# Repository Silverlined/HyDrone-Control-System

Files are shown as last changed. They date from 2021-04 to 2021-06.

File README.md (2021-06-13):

## About the project

This project follows the develepoment of a control system for an unmanned surface vehicle (USV).
It consists of efficient code to read the PWM output of an RC receiver via Pin Change Interrupts and write PWM to the ESCs controlling underwater thrusters.
An IMU sensor is used to keep track of the vehicle's orientation, while Time-of-Flight (ToF) sensors measure the distance to canal walls and control the orientation via PID algorithm.

## Introduction

Inspection of bridges and quay walls, below or above the water line, is the main activity of oQuay.
They conduct inspection in different ways but one of their key instruments is a sonar camera attached to a USV, called the HyDrone.
In order to make recordings of high quality it is important to sail the HyDrone at a constant distance (parallel) to quay walls.
During operation, the position of the vehicle is affected by wind and water currents, making the sonar images blurry.
The lack of a control system to correct the HyDrones orientation is a pitfall in the design and affects the quality of the inspection work.
Moreover, the GoPro camera on the HyDrone has a short transmission range of ~10m.
This becomes a problem when the HyDrone sails further away, losing the video feedback and the control over the camera.
oQuay are looking for something that can guarantee control of the movement of the vehicle and a device that can increase the transmission range of their GoPro camera.

Assembly files are in the relevant repositoty folders.

## MuSCoW

| Must haves | Should haves | Could haves |
|---|---|---|
| Independent adjustment of the orientation of the HyDrone with respect to canal walls | Orientation correction should be smooth with no oscillations | Adjustment mechanism to adapt for different situations - different heights and shapes of canal walls |
| Sailing at a constant distance 70cm~1m | Stable response in spite of wind and water currents | Audible feedback from the control commands - start/stop could be indicated with some type of sound |
| Increased video transmission range to at least 100 meters | Validation with experiments in real canal environment | |
| Increased GoPro control range to at least 100 meters | Developed system should be portable and detachable | |
| Control system must not exceed €100 | Power source of the system should be rechargeable | |
| Real-time transmission of the video signal | Video should be shown on one of the already available displays | |

## Planning

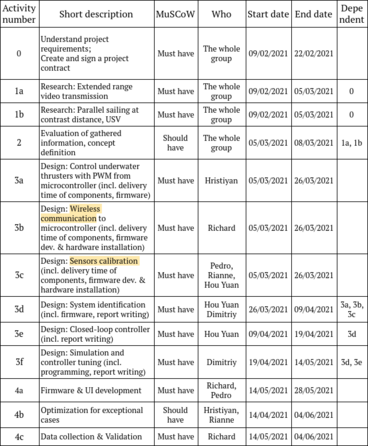
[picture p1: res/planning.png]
Plan


## Pin Change Interrupts

```c
PCICR |= (1 << PCIE0);   // set PCIE0 bit to to enable PCMSK0 scan
PCMSK0 |= (1 << PCINT0); // set PCINT0 (digital pin 8) to trigger an interrupt on state change

// PCINT0_vect is the compiler vector for PCINT0 on PORTB of ATmega328
ISR(PCINT0_vect)
{
  //    // Channel 1==================================
  if (last_channel_1_state == 0 && PINB & B00000001)
  {
    last_channel_1_state = 1;
    timer_channel_1 = micros();
  }
  if (last_channel_1_state == 1 && !(PINB & B00000001))
  {
    last_channel_1_state = 0;
    receiver_input_channel_1 = micros() - timer_channel_1;
  }
  ...
}
```

## FPV System

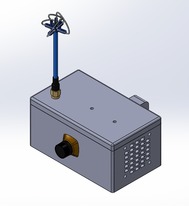
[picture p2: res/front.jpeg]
front


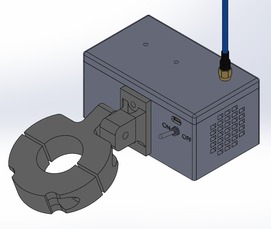
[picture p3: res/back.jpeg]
back


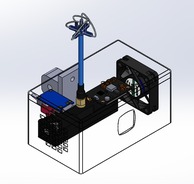
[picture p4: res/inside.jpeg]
inside


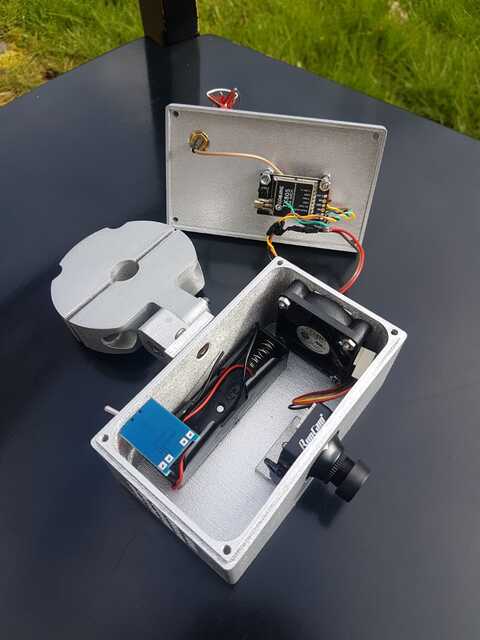
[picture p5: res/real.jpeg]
real


## Control System

### Heading determination system (HDS)

- Microcontroller
- IMU, 3-DoF Gyroscope

Angular velocity is:

`ω = Δφ/Δt = (φn − φn−1)/(tn − tn−1)`

Current angle can be calculated from previous angle as:

`φn = φn−1 + ω·Δt`

```c
float angle = 0;  /* or any initial value */
while(1){
    float omega = getAngularVelocity();
    angle += omega * timestep;
}
```

provided that the function `getAngularVelocity` returns a value regularly at timestep intervals. For example, 100 Hz.

### Modelling
Develop a simple MEMS gyro model in Python; Second-order process dead time.
The model can be used to test out the linear control system design in a non-linear simulated environment.
This is especially handy for tweaking control parameters without having to load software onto the embedded device and test it repeatedly physically.
The model can also be applied to check the stability of the designed controller.

```τ2 d2ydt2 + 2ζ τ dydt + y = Kp u(t−θp)```

```py
Kp = 2.26   # Process gain
tau = 0.17  # Time constant, normalized 0-1
theta = -0.03  # Dead time, normalized 0-1
zeta = 0.72    # Damping ratio
```

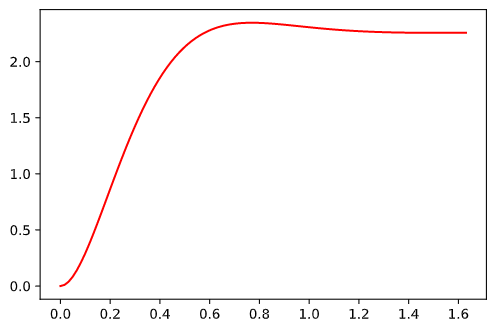
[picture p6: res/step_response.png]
step


### ToF sensors

- I2C
- Arduino Nano (Atmega328) has a single hardware UART. Software UART requires dedicating PCINT (pin change interrupts)

### Raspberry Pi Workflow

1. Install arduino-cli:

```
curl -fsSL https://raw.githubusercontent.com/arduino/arduino-cli/master/install.sh | sh
arduino-cli config init
```

2. Add to PATH: (edit .bashrc)

```export PATH=$PATH:/home/pi/bin```

3. Copy Arduino Libraries: (~/Arduino/libraries/)

4. Compile & Upload

```
arduino-cli core update-index
arduino-cli core install arduino:avr
arduino-cli compile -b arduino:avr:nano file_path
arduino-cli upload -p /dev/ttyACM0 -b arduino:avr:nano file_path
```

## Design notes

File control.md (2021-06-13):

# Heading determination system (HDS)

- Microcontroller
- IMU, 3-DoF Gyroscope

Angular velocity is:

`ω = Δφ/Δt = (φn − φn−1)/(tn − tn−1)`

Current angle can be calculated from previous angle as:

`φn = φn−1 + ω·Δt`

```c
double angle = 0;  /* or any initial value */
while(1){
    double omega = get_angular_velocity();
    angle += omega * timestep;
}
```

provided that the function get_angular_velocity returns a value regularly at timestep intervals.

Develop a simply MEMS gyro model in Python.
The model can be used to test out the linear control system design in a non-linear simulated environment.
This is especially handy for tweaking control parameters without having to load software onto the embedded device and test it repeatedly physically.
The model can also be applied to check the stability of the designed system.

# ToF sensors

- I2C
- Arduino Nano (Atmega328) has a single hardware UART. Software UART requires dedicating PCINT (pin change interrupts)

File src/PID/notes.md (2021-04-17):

# PID

## Continuous to Discrete time representation
- Via *Tustin transform*

1. Derivative amplifies HF noise;
> Low Pass filer the signal before/after taking the derivative.
2. Derivative "kick" during setpoint change;
> Derivative-on-measurement, not errro.
3. Integrator can saturate output;
> Integrator anti-windup.
4. Limits on system input amplitude;
> Clamp controll output.
5. Choosing a sample time T
> Sample time of the controller to be 10 times higher than the system's.

## Code Structure:

- Header-file
> #include "pid.h"
- PID controller struct
> contains gains, storage variables, etc.
- Initialisation function
> set gains, sample time, etc.
- Update function
> provide setpoint and measurement, returns contorller output.

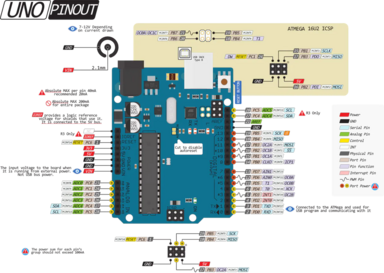
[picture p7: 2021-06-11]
res/arduino_uno_pinout_3YIbUj4F2o.png

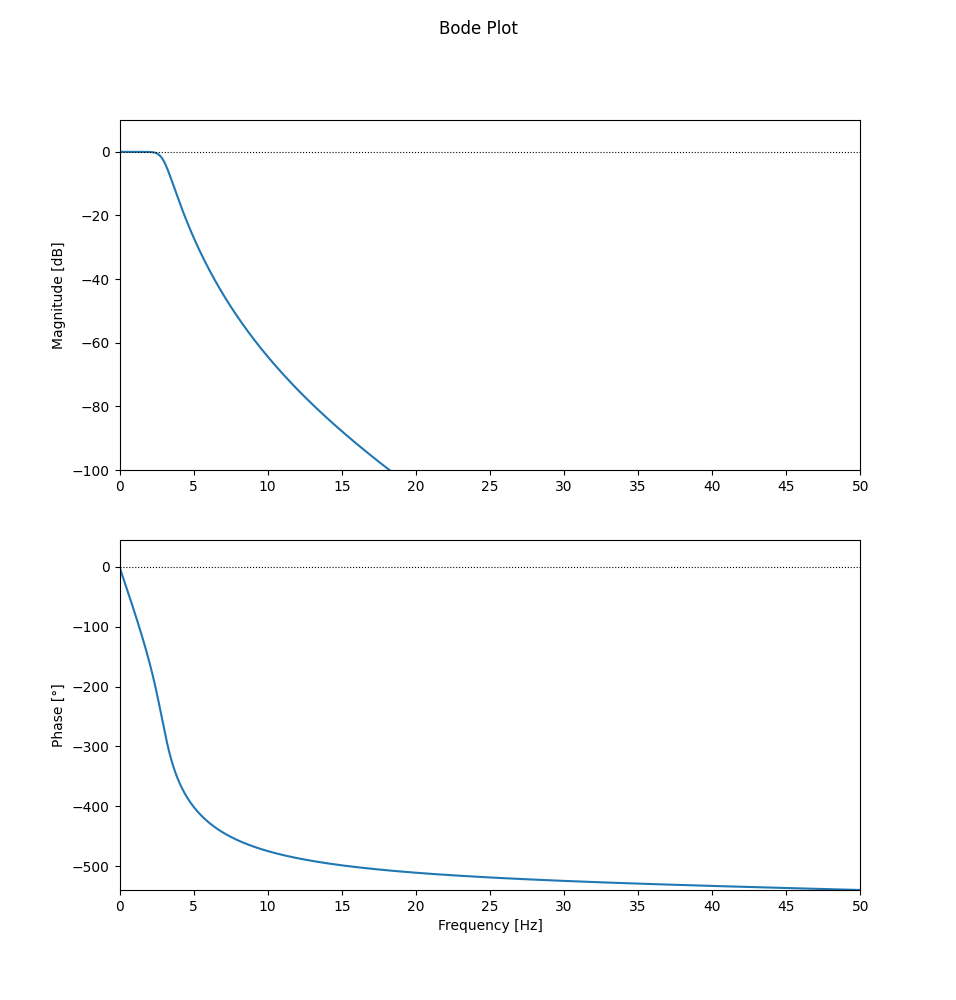
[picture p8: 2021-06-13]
res/lowpass_3Hz.png

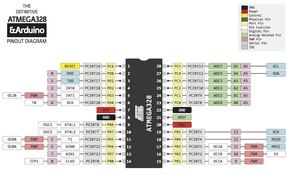
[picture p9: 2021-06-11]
res/Atmega328P-PU-DIP-28.jpg

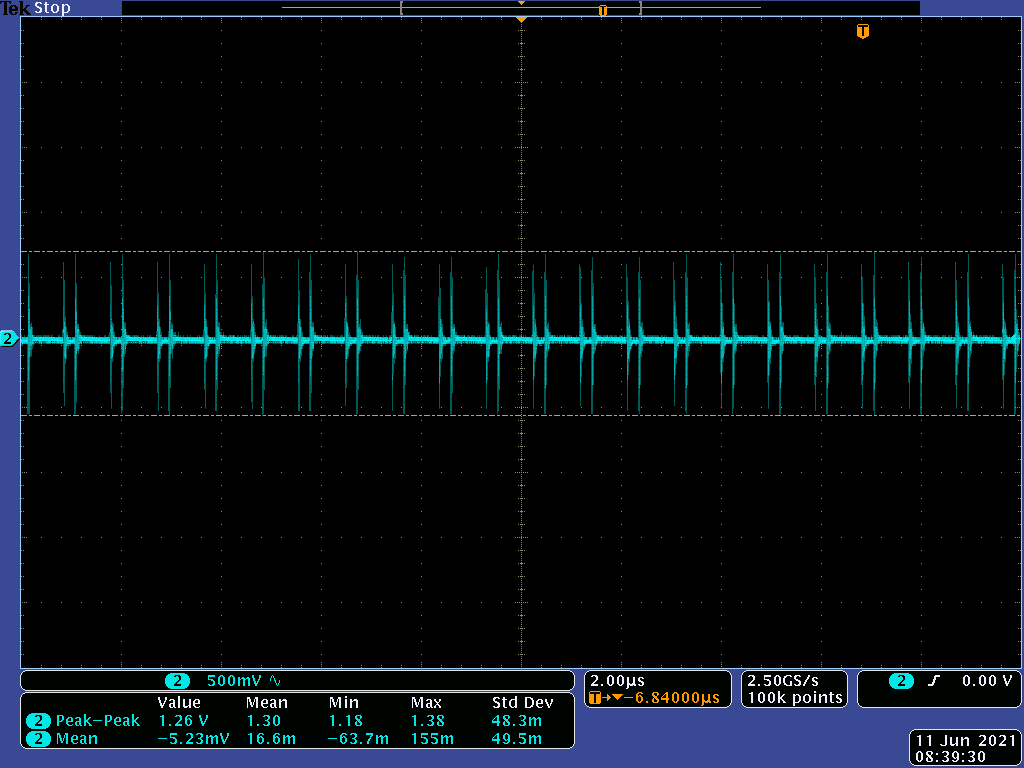
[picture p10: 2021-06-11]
res/tek00007.png

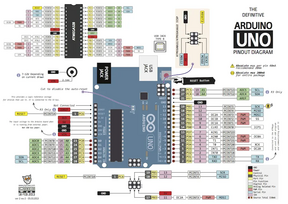
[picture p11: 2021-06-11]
res/ARDUINO_V2.png

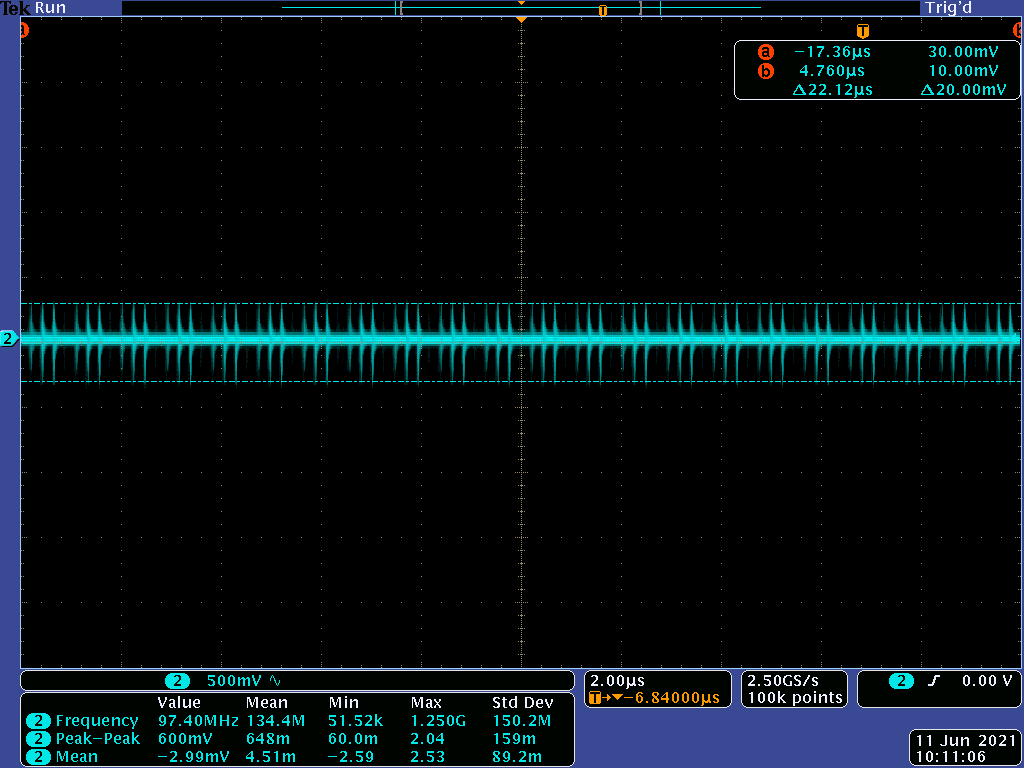
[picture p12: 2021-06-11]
res/tek00011.png

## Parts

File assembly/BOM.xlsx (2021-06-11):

Part Description | Manufacturer | Part Number | Quantity | Price (€) | Sub-Total (€)
FPV Receiver (https://www.banggood.com/Eachine-RC832-5_8Ghz-48CH-Wireless-Raceband-AV-Boscam-FPV-Receiver-p-975426.html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) | Eachine | RC832 | 1 | 19.71 | 19.71
FPV Transmitter (https://www.banggood.com/Eachine-TX805-5_8G-40CH-25-or-200-or-600-or-800mW-FPV-Transmitter-TX-LED-Display-Support-OSD-or-Pitmode-or-Smart-Audio-p-1333984.html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) | Eachine | TX805 | 1 | 17.96 | 17.96
FPV Camera (https://www.banggood.com/RunCam-Swift-2-600TVL-1-or-3-CCD-2_5mm-or-2_3mm-or-2_1mm-FOV-130-or-150-or-165-Degree-Mini-FPV-Camera-PAL-with-MIC-Support-OSD-p-1118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) | RunCam | Swift 2 | 1 | 27.78 | 27.78
Antennas (https://www.banggood.com/1-Pair-Aomway-5_8GHz-3dBi-4-Leaf-Clover-RHCP-FPV-Antenna-SMA-or-RP-SMA-w-or-Canopy-for-RC-Drone-Goggles-Monitor-p-961730.html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) | Aomway | 4 Leaf Clover | 1 | 12.67 | 12.67
RCA to HDMI Converter (https://www.banggood.com/Mini-Composite-AV-CVBS-Video-Adapter-720p-1080p-RCA-to-HDMI-Converter-p-1759725.html?ID=6287845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) |  |  | 1 | 6.66 | 6.66
Shipping cost |  |  |  | ~11 | 11
 |  |  |  | Total | 95.78

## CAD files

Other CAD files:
assembly/Drawings/Box.SLDDRW
assembly/Drawings/Camera Spacer Block.SLDDRW
assembly/Drawings/Connector Adapter Plate.SLDDRW
assembly/Drawings/Fixture 1.SLDDRW
assembly/Drawings/Fixture 2.SLDDRW
assembly/Drawings/Fixture 3.SLDDRW
assembly/Drawings/Hook Side.SLDDRW
assembly/Drawings/Intake Cover.SLDDRW
assembly/Drawings/Lid.SLDDRW
assembly/Drawings/Sensor Fixation Piece.SLDDRW

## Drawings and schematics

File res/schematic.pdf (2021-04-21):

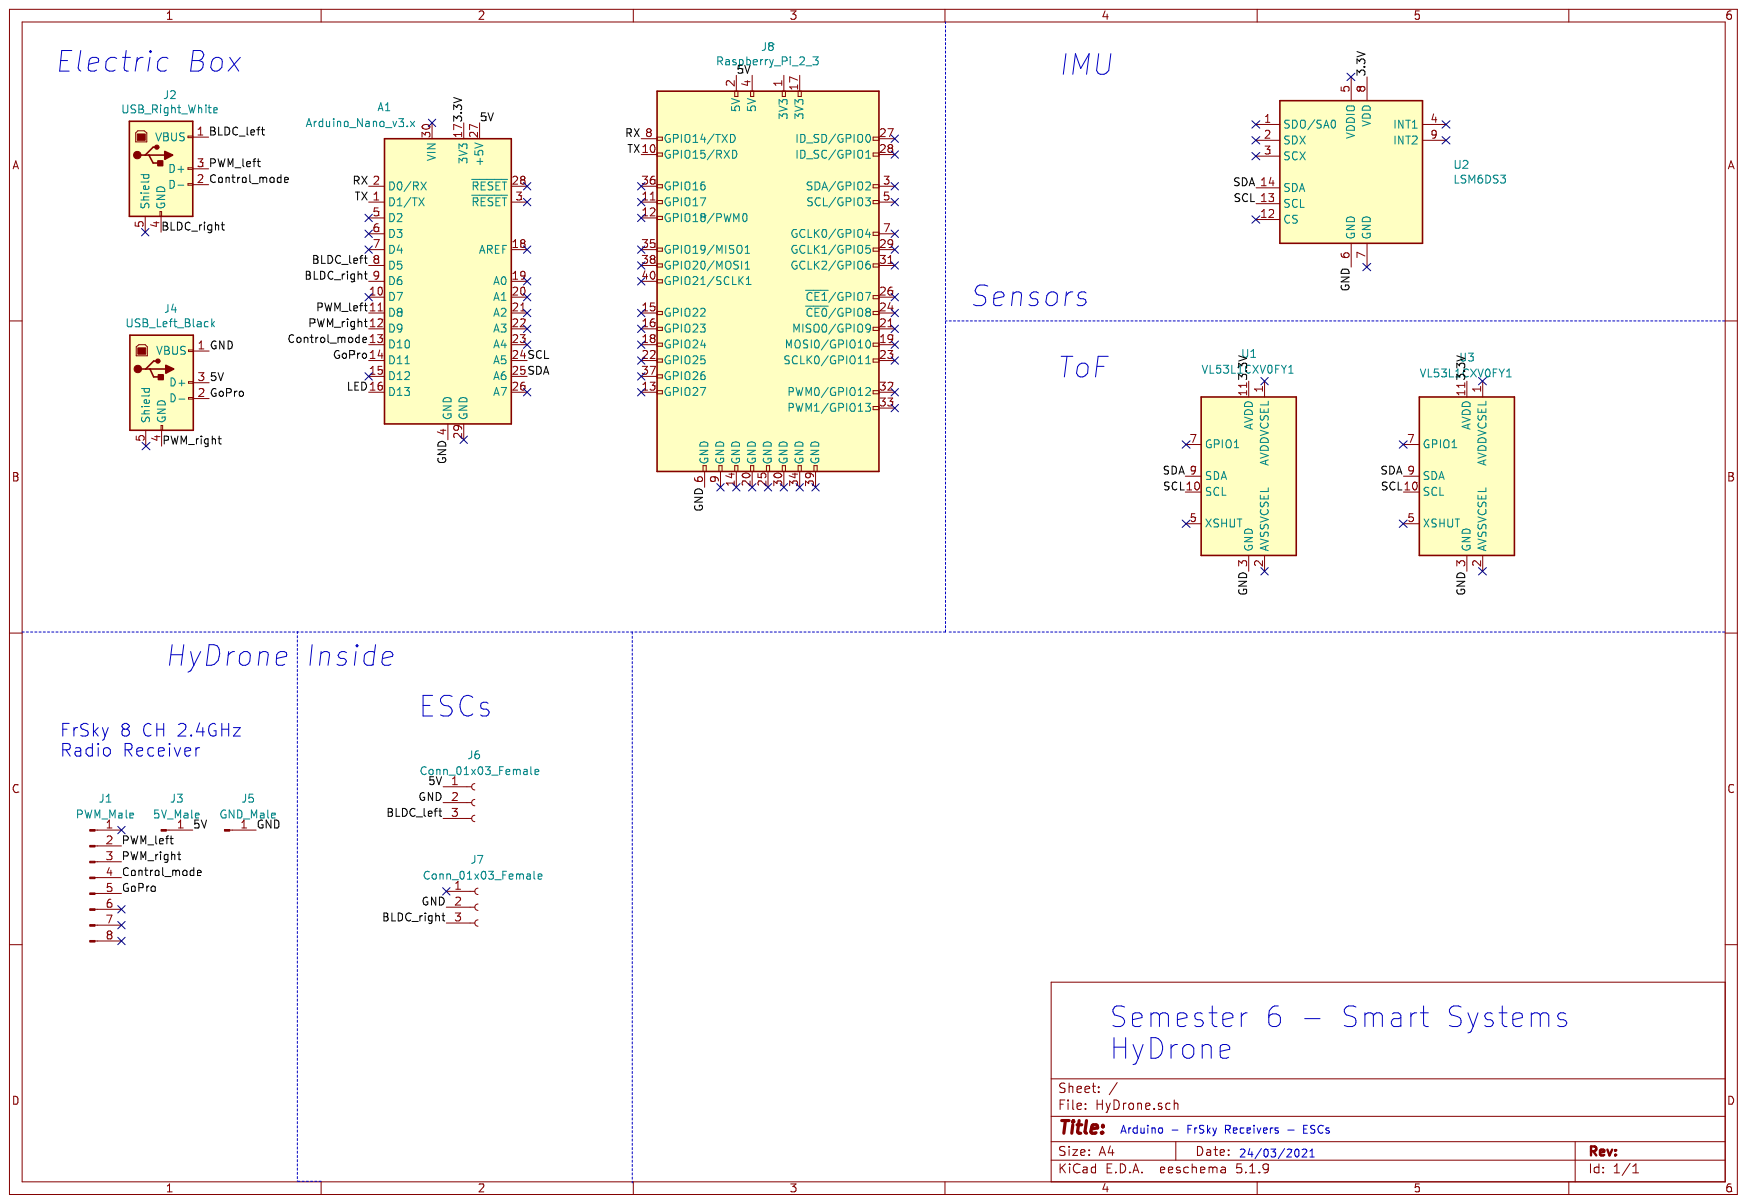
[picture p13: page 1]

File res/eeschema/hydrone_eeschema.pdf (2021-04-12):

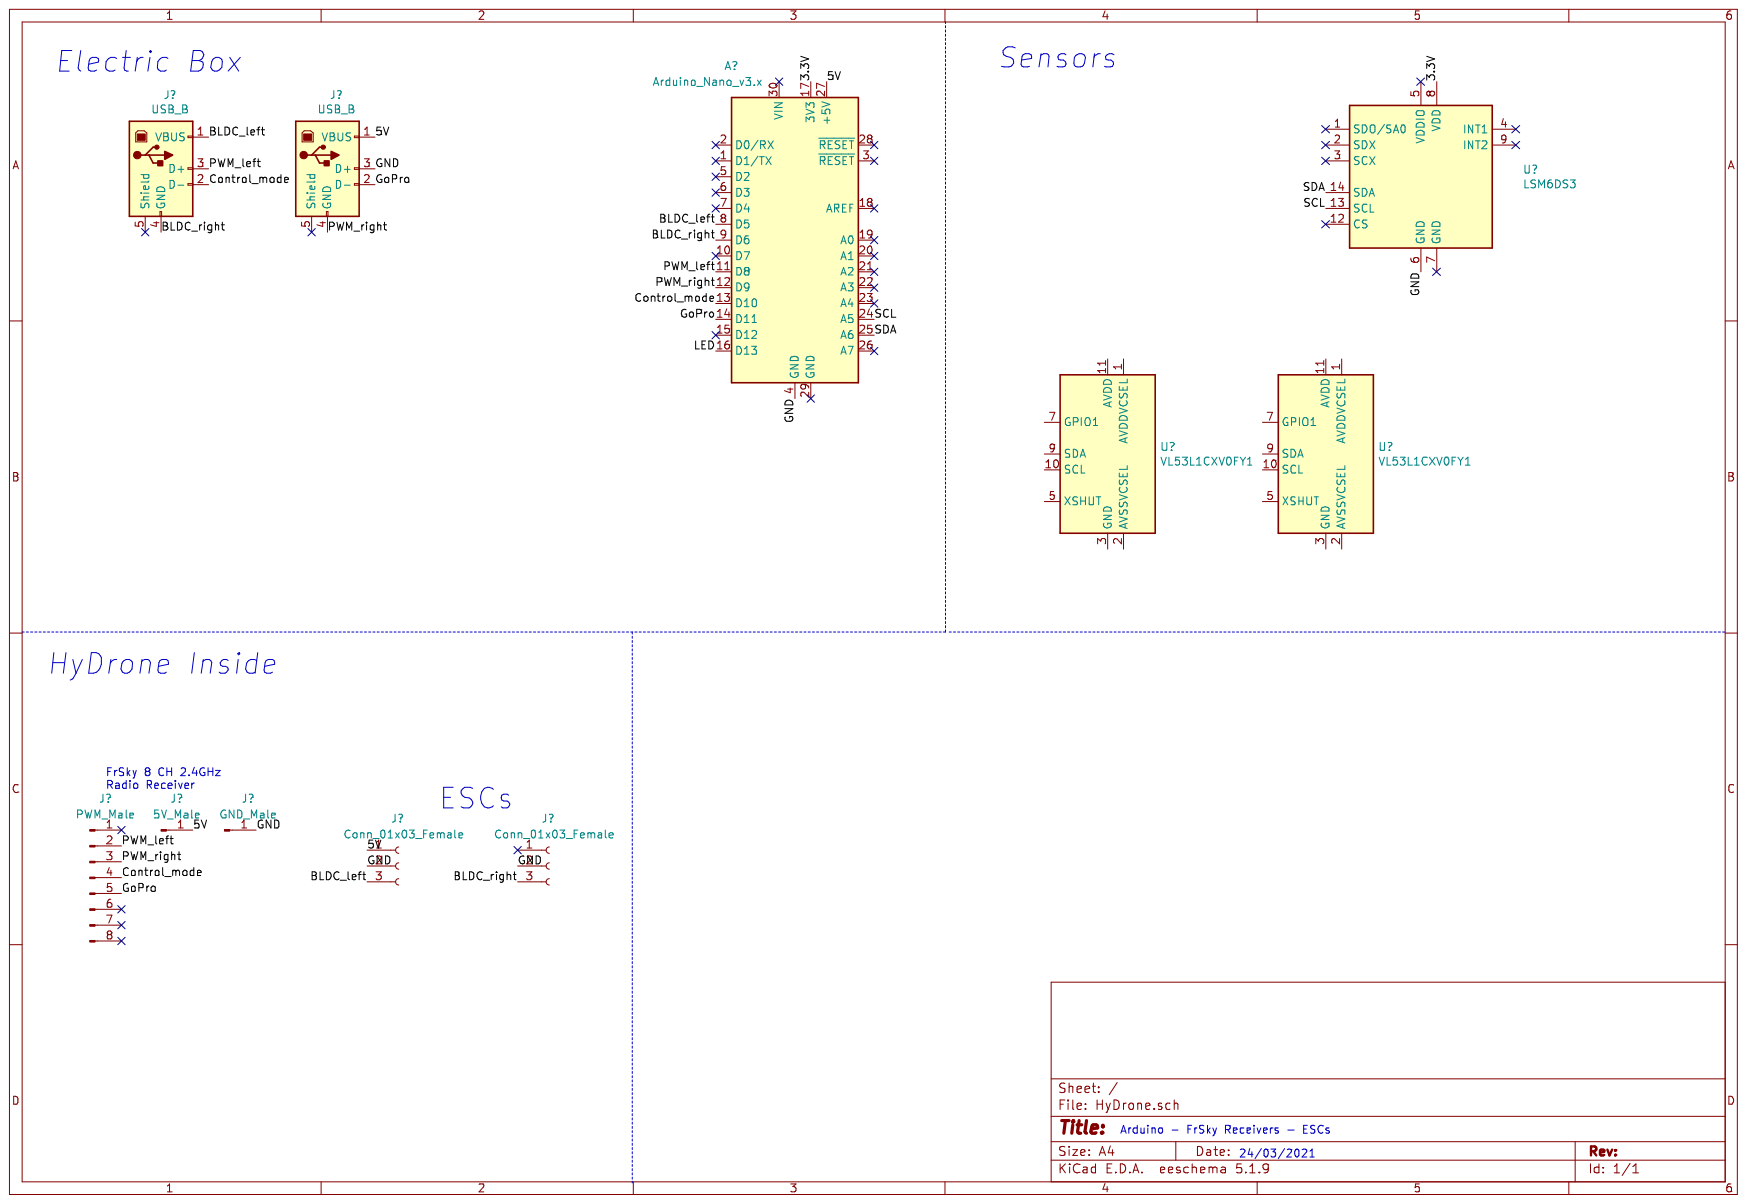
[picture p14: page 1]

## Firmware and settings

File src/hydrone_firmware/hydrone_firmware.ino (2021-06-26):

// Libs for HyDrone Controll
#include <Servo.h>
#include <SparkFunLSM6DS3.h>
#include <Wire.h>
#include "PollTimer.h"

// Libs for ToF sensor
#include <ComponentObject.h>
#include <RangeSensor.h>
#include <SparkFun_VL53L1X.h>
#include <math.h>
#define TCAADDR 0x70
#define DISTANCE_45 0   // connected to serial bus 0
#define DISTANCE_90 1

// Libs for filtering
#include <Filters.h>
#include <AH/Timing/MillisMicrosTimer.hpp>
#include <Filters/Butterworth.hpp>

// Sampling frequency
const float f_s_gyro = 100; // [Hz]
const float f_s_tof = 10; // [Hz]
// Cut-off frequency (-3 dB)
const float f_c_gyro = 3;
const float f_c_tof = 1;
// Normalized cut-off frequency
const float f_n_gyro = 2 * f_c_gyro / f_s_gyro;
const float f_n_tof = 2 * f_c_tof / f_s_tof;

auto filterGyro = butter<6>(f_n_gyro);
auto filterToF = butter<6>(f_n_tof);

PollTimer gyroTimer(100); // [Hz]
PollTimer pidTimer(10);   // [Hz]

SFEVL53L1X distance;

void tcaselect(uint8_t i) {   // switches between different i2c busses.
  if (i > 7) return;

  Wire.beginTransmission(TCAADDR);
  Wire.write(1 << i);
  Wire.endTransmission();
}

#define UPPER_THRESHOLD 1520
#define LOWER_THRESHOLD 1480
#define DEBUG 1
#define LED 13

bool isRecording = false; 
// IMU config
LSM6DS3 imu_sensor(I2C_MODE, 0x6B);
//const float GYRO_CALIBRATION[3] = {0, 0, 0};
//const float ACCEL_CALIBRATION[3] = {0, 0, 0};
const float GYRO_CALIBRATION[3] = {0.12, -0.06, -0.14};
const float ACCEL_CALIBRATION[3] = {0.0, 0.0, 0.0};

uint16_t init_time;
const uint16_t TIME_STEP_MICROS = 10000; // 10 ms period -> 100 Hz sampling rate.
unsigned long previousTime = 0;

// Calibrated pulse width for FrSky Taranis Q X7 16CH 2.4Ghz transmitter with RX8R receiver
const uint16_t RC_min[4] = {1000, 1000, 1000, 1000};
const uint16_t RC_mid[4] = {1500, 1500, 1500, 1500};
const uint16_t RC_max[4] = {2000, 2000, 2000, 2000};

uint8_t last_channel_1_state = 0, last_channel_2_state = 0, last_channel_3_state = 0, last_channel_4_state = 0;
uint16_t receiver_input_channel_1, receiver_input_channel_2, receiver_input_channel_3, receiver_input_channel_4;
uint32_t timer_channel_1, timer_channel_2, timer_channel_3, timer_channel_4;

uint32_t last_rc_update = 0;
Servo motor_left, motor_right, control_toggle_left, gopro_toggle_right;

float orientation = 0; // Orientation of the HyDrone

const float dt = 0.01; // 100 [Hz]
const float Kp = 2;
const int dWall = 700; // [mm]
const int wallLead = 2000; // [mm]
const int speed = 1600; // [micro seconds, Pulse]

// Interrupt service routine called evey time digital input pin 8, 9, 10, or 11 changes state
// PCINT0_vect is the compiler vector for PCINT0 on PORTB of ATmega328
ISR(PCINT0_vect)
{
  //    // Channel 1==================================
  if (last_channel_1_state == 0 && PINB & B00000001)
  {
    last_channel_1_state = 1;
    timer_channel_1 = micros();
  }
  if (last_channel_1_state == 1 && !(PINB & B00000001))
  {
    last_channel_1_state = 0;
    receiver_input_channel_1 = micros() - timer_channel_1;
  }
  // Channel 2==================================
  if (last_channel_2_state == 0 && PINB & B00000010)
  {
    last_channel_2_state = 1;
    timer_channel_2 = micros();
  }
  if (last_channel_2_state == 1 && !(PINB & B00000010))
  {
    last_channel_2_state = 0;
    receiver_input_channel_2 = micros() - timer_channel_2;
  }
  //    // Channel 3==================================
  if (last_channel_3_state == 0 && PINB & B00000100)
  {
    last_channel_3_state = 1;
    timer_channel_3 = micros();
  }
  if (last_channel_3_state == 1 && !(PINB & B00000100))
  {
    last_channel_3_state = 0;
    receiver_input_channel_3 = micros() - timer_channel_3;
  }
  //    // Channel 4==================================
  if (last_channel_4_state == 0 && PINB & B00001000)
  {
    last_channel_4_state = 1;
    timer_channel_4 = micros();
  }
  if (last_channel_4_state == 1 && !(PINB & B00001000))
  {
    last_channel_4_state = 0;
    receiver_input_channel_4 = micros() - timer_channel_4;
  }
}

//Subroutine for displaying the receiver signals
//Subroutine for displaying the receiver signals
void readReceiverSignals()
{
  Serial.print("Channel 1:");
  if (receiver_input_channel_1 - LOWER_THRESHOLD < 0)
    Serial.print("<<<");
  else if (receiver_input_channel_1 - UPPER_THRESHOLD > 0)
    Serial.print(">>>");
  else
    Serial.print("-+-");
  Serial.print(receiver_input_channel_1);

  Serial.print("  Channel 2:");
  if (receiver_input_channel_2 - LOWER_THRESHOLD < 0)
    Serial.print("^^^");
  else if (receiver_input_channel_2 - UPPER_THRESHOLD > 0)
    Serial.print("vvv");
  else
    Serial.print("-+-");
  Serial.print(receiver_input_channel_2);

  Serial.print("  Channel 3:");
  if (receiver_input_channel_3 - LOWER_THRESHOLD < 0)
    Serial.print("vvv");
  else if (receiver_input_channel_3 - UPPER_THRESHOLD > 0)
    Serial.print("^^^");
  else
    Serial.print("-+-");
  Serial.print(receiver_input_channel_3);

  Serial.print("  Channel 4:");
  if (receiver_input_channel_4 - LOWER_THRESHOLD < 0)
    Serial.print("<<<");
  else if (receiver_input_channel_4 - UPPER_THRESHOLD > 0)
    Serial.print(">>>");
  else
    Serial.print("-+-");
  Serial.println(receiver_input_channel_4);
}

void inputStep()
{
  long _timer_10s = micros() + 10000000;
  Serial.print(F("Begin"));
  Serial.println("");
  delay(200);
  while (_timer_10s > micros())
  {
    /// Begin Step input
    motor_left.writeMicroseconds(1750);
    motor_right.writeMicroseconds(1250);

    /// Collect IMU data, disable pin change interrupts
    if (micros() - previousTime > TIME_STEP_MICROS)
    {
      getData();
    }
  }
  Serial.print(F("Stop"));
  Serial.println("");
}

void getData()
{
  //millis() is not suitable for precise timing as it has a lot of jitter
  previousTime = micros();
  PCICR &= ~(1 << PCIE0);   /// Disable Pin Change Interrupts
  Serial.print(F("Data:"));
  Serial.print(imu_sensor.readFloatAccelX() - ACCEL_CALIBRATION[0], 4);
  Serial.print(",");
  Serial.print(imu_sensor.readFloatAccelY() - ACCEL_CALIBRATION[1], 4);
  Serial.print(",");
  Serial.print(imu_sensor.readFloatAccelZ() - ACCEL_CALIBRATION[2], 4);
  Serial.print(",");
  Serial.print(imu_sensor.readFloatGyroX() - GYRO_CALIBRATION[0], 4);
  Serial.print(",");
  Serial.print(imu_sensor.readFloatGyroY() - GYRO_CALIBRATION[1], 4);
  Serial.print(",");
  Serial.print(imu_sensor.readFloatGyroZ() - GYRO_CALIBRATION[2], 4);
  Serial.println("");
  PCICR |= (1 << PCIE0); /// Enable Pin Change Interrupts
}

void initDistanceSensors() 
{
  //Initialize ToF sensors
  tcaselect(DISTANCE_45);
  if (distance.begin() != 0)
  {
    Serial.println("Failed to initialize ToF 90. Waiting...");
    while (1);
  }
  distance.setDistanceModeLong(); 

  tcaselect(DISTANCE_90);
  if (distance.begin() != 0)
  {
    Serial.println("Failed to initialize ToF45. Waiting...");
    while (1);
  }
  distance.setDistanceModeLong(); 
}

int getDistance(int sensor_id) {  // gets ToF sensor
  tcaselect(sensor_id);

  distance.startRanging(); //Write configuration bytes to initiate measurement
  while (!distance.checkForDataReady());
  int distance_val = distance.getDistance(); //Get the result of the measurement from the sensor
  distance.clearInterrupt();
  distance.stopRanging();

  return distance_val;
}

int getOrientationError(int d90, int d45) {
  float angle = orientation * DEG_TO_RAD;
  float l = cos(angle) * d90;
  float p = l - dWall;
  float beta = atan2(p, wallLead);
  
  return (beta - angle) * RAD_TO_DEG;
}

int clamp(int pwm) {
  if (pwm < 980 || pwm >2020) {
      pwm = 1500;
    }
    return pwm;
}

void setup()
{
  // ATmega pins default to inputs, therefore there is no need to use the pinMode function
  PCICR |= (1 << PCIE0);   // set PCIE0 bit to to enable PCMSK0 scan
  PCMSK0 |= (1 << PCINT0); // set PCINT0 (digital pin 8) to trigger an interrupt on state change
  PCMSK0 |= (1 << PCINT1); // set PCINT0 (digital pin 9) to trigger an interrupt on state change
  PCMSK0 |= (1 << PCINT2); // set PCINT0 (digital pin 10) to trigger an interrupt on state change
  PCMSK0 |= (1 << PCINT3); // set PCINT0 (digital pin 11) to trigger an interrupt on state change

  Serial.begin(115200);
  Wire.begin();
  delay(500);
  if ( imu_sensor.begin() != 0 ) {
    Serial.print(F("Failed to detect IMU\n"));
    while (1);
  }
  else Serial.print(F("IMU initialized\n"));

  // Accelerometer Config
  imu_sensor.settings.accelEnabled = 0;

  // Temp Config
  imu_sensor.settings.tempEnabled = 0;

  // Gyro Config
  imu_sensor.settings.gyroEnabled = 1;
  imu_sensor.settings.gyroRange = 125;      // [dps].  Can be: 125, 245, 500, 1000, 2000
  imu_sensor.settings.gyroSampleRate = 104; // [Hz].  Can be: 13, 26, 52, 104, 208, 416, 833, 1666
  imu_sensor.settings.gyroFifoEnabled = 0;


  motor_left.attach(5, RC_min[1], RC_max[1]);
  motor_right.attach(6, RC_min[2], RC_max[2]);

  initDistanceSensors();  // Initialize Time of Flight Sensors

  gyroTimer.start();
  pidTimer.start();
  init_time = micros();
  delay(500);
}

void loop()
{
  if (receiver_input_channel_3 > UPPER_THRESHOLD && !isRecording)
  {
    //inputStep();
    Serial.print(F("Begin"));
    Serial.println("");
    isRecording = true;
    delay(200);
  } else if (receiver_input_channel_3 < LOWER_THRESHOLD && isRecording) 
  {
    Serial.print(F("Stop"));
    Serial.println("");
    isRecording = false;
    delay(200);
  }
  
  if (receiver_input_channel_4 > UPPER_THRESHOLD) {
    if(gyroTimer.check()) 
    {
      float yaw_rate = imu_sensor.readFloatGyroZ() - GYRO_CALIBRATION[2];
      yaw_rate = filterGyro(yaw_rate);
      if (abs(yaw_rate) > 0.05) {
        orientation += yaw_rate * dt;
        Serial.print(F("Orientation:"));
        Serial.println(orientation);
      }
    }

    if (pidTimer.check())
    {
      int distance45 = getDistance(DISTANCE_45);
      int distance90 = filterToF(getDistance(DISTANCE_90));
 
      float error = getOrientationError(distance90, distance45);
      if (abs(error) < 5) error = 0;
      if (error > 30) error = 30;
      if (error < -30) error = -30;
      

      float out = Kp * error;
      Serial.println(out);
      if (out > 0) {
        motor_left.writeMicroseconds(speed - out);
        motor_right.writeMicroseconds(speed + out);
      } else if (out < 0) {
        motor_left.writeMicroseconds(speed + out);
        motor_right.writeMicroseconds(speed - out);
      } else {
        motor_left.writeMicroseconds(speed);
        motor_right.writeMicroseconds(speed);
      }
      
      if (DEBUG) {
        Serial.println("Distance 1: " + String(distance45) + "\tDistance 2: " + String(distance90));
      }
    }
    return;
  }
  
  orientation = 0;
  if (millis() - last_rc_update > 25)
  {
    receiver_input_channel_1 = clamp(receiver_input_channel_1);
    receiver_input_channel_2 = clamp(receiver_input_channel_2);
    motor_left.writeMicroseconds(receiver_input_channel_1);
    motor_right.writeMicroseconds(receiver_input_channel_2);
    last_rc_update = millis();

    if (DEBUG)
    {
      readReceiverSignals();
      delay(250);
    }
  }
}

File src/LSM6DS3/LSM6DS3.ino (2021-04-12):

#include <SparkFunLSM6DS3.h>
#include <Wire.h>
//#include <SPI.h>

LSM6DS3 imu_sensor( I2C_MODE, 0x6B );
//LSM6DS3 imu_sensor( SPI_MODE, 10 );


uint16_t init_time;
const uint16_t TIME_STEP_MICROS = 10400; // 10 ms period -> 100 Hz sampling rate.
unsigned long previousTime = 0;

void setup() {
  Serial.begin(115200);
  Wire.begin();
  delay(500);
  if ( imu_sensor.begin() != 0 ) {
    Serial.print("Failed to detect IMU\n");
    while (1);
  }
  else Serial.print("IMU initialized\n");

  // Accelerometer Config
  imu_sensor.settings.accelEnabled = 1;
  imu_sensor.settings.accelRange = 8;      //Max G force readable.  Can be: 2, 4, 8, 16
  imu_sensor.settings.accelSampleRate = 104;  //Hz.  Can be: 13, 26, 52, 104, 208, 416, 833, 1666, 3332, 6664, 13330
  imu_sensor.settings.accelBandWidth = 200;  //Hz.  Can be: 50, 100, 200, 400;
  imu_sensor.settings.accelFifoEnabled = 0; 
  
  // Gyro Config
  imu_sensor.settings.gyroEnabled = 1;
  imu_sensor.settings.gyroRange = 125;   // [dps].  Can be: 125, 245, 500, 1000, 2000
  imu_sensor.settings.gyroSampleRate = 104;   // [Hz].  Can be: 13, 26, 52, 104, 208, 416, 833, 1666
  imu_sensor.settings.gyroFifoEnabled = 0;

  // Temp
  imu_sensor.settings.tempEnabled = 0;

  init_time = micros();
  delay(500);
}

// Spikes in IMU data can be caused by the code trying to read the sensor registers while they are being written.
// The IMU has 2 interrupt pins which can be used to see when new data is available to mitigate this issue. 

void loop() {
  if (micros() - previousTime > TIME_STEP_MICROS) { //millis() is not suitable for precise timing as it has a lot of jitter
    previousTime = micros();
    Serial.print(F("Data:"));
    Serial.println(imu_sensor.readFloatAccelX(), 4); //Serial.print(",");
//    Serial.print(imu_sensor.readFloatAccelY(), 4); Serial.print(",");
//    Serial.print(imu_sensor.readFloatAccelZ(), 4); Serial.print(",");
//    Serial.print(imu_sensor.readFloatGyroX(), 4); Serial.print(",");
//    Serial.print(imu_sensor.readFloatGyroY(), 4); Serial.print(",");
//    Serial.print(imu_sensor.readFloatGyroZ(), 4); Serial.println("");
  }
}

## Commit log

2021-03-04 Add PWM receiver read function
2021-03-29 Add schematc
    [HyDrone.sch]
2021-04-12 Add Gyro
2021-04-14 Add IMU
2021-04-14 Add Raspberry Pi Data Collection script
2021-04-16 Calibrate Gyro/Accel, Add input step control
2021-04-17 Add PID
2021-04-21 Add schematic
2021-06-11 src: Add ToF sensors
    [BOM.xlsx]
2021-06-12 Add P regulator
2021-06-13 src: add low-pass filter
2021-06-13 build: deploy on raspberry pi
2021-06-15 src: clamp inputs, p gain
2021-06-26 add drawings
    [Box.SLDDRW, Camera Spacer Block.SLDDRW, Fixture 1.SLDDRW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]
